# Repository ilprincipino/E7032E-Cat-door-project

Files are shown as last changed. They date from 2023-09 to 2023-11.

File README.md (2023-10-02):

# E7032E-Cat-door-project
Universal low power antennas for pet microchips
<p>
  
**Project members:** <br>
Matilda Segerlund, matseg-9@student.ltu.se  <br>
Nebez Rashid, nabras-9@student.ltu.se <br>
Anders Hagström, hagane-9@student.ltu.se <br>
Agnes Lindsten, agelin-7@student.ltu.se <br>
Arvid Mattsson, arvmat-9@student.ltu.se <br>
Jakob Ekvall, jakekv-9@student.ltu.se <br>

Link to report: [https://www.overleaf.com/read/vsyjcxfwmcch](https://www.overleaf.com/read/vsyjcxfwmcch) <br>

Link to presentation: https://docs.google.com/presentation/d/12QPiXXhClUaFdsH-6-YMc6YWno67U1GOmlV3GwxZOh8/edit?usp=sharing

Link to WBS/project plan: https://docs.google.com/spreadsheets/d/1j_RC8x2nzi24WwkHtlm5jIMLNItzt1e427vKWdE4rbc/edit?usp=sharing <br>

**Background:** <br>
Since the mid-80's, microchip implants have been used in pets and livestocks to identify them. These implements are a little larger than a rice grain. They are passive RFID chips that must be remotely powered to receive the identification information. They are progressively been required by law. <br>

Beside legal identification, these microchips can be used to identify a pet when they want to be fed (i.e., not allow an obese pet to over eat) or to let them enter or exit their home. The latter prevents "foreign" cats to enter homes where they have no business to be in. <br>

There is a problem when the orientation of the scanner's antenna and the microchips are not aligned. The pet doors and feeders are battery powered and fixed. The former results in not enough power to retrieve the information, while the latter could have been a solution by rotating the antenna (or chip inside the pet). <br>

**Objective:** <br>
The project is simply to design a low power antenna that allows the microchip to be read whatever is its relative orientation. <br>

**Key features:** <br>
* **Compatibility:** The solution must be ISO 11784 and ISO 11785 compliant. That is, it must be able to be optimized for 134.2 kHz, but should also be able to read at 125 kHz for US microchips.
* **Low power:** The cat door should work 6 months on four AA batteries.
* **Size:** It should fit in a pet door.
* **Temperature:** It should function in temperatures from -20°C to 60°C.
* **Internet ready:** The solution should be able to integrate a secured solution that connects to the Internet. This could include near field communication (NFC), bluetooth, and WiFi solutions. 

</p>

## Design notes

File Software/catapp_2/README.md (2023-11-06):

# catapp_2

A new Flutter project.

## Getting Started

This project is a starting point for a Flutter application.

A few resources to get you started if this is your first Flutter project:

- [Lab: Write your first Flutter app](https://docs.flutter.dev/get-started/codelab)
- [Cookbook: Useful Flutter samples](https://docs.flutter.dev/cookbook)

For help getting started with Flutter development, view the
[online documentation](https://docs.flutter.dev/), which offers tutorials,
samples, guidance on mobile development, and a full API reference.

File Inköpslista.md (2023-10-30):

| Date | Item |Amount | Link | Approved/ordered | Received | 
|---|---|---|---|---|---|
| 3/10 |Raspberry Pico W | 2 |https://www.electrokit.com/produkt/raspberry-pi-pico-wh/ | <ul><li>[X] </li></ul>  | <ul><li>[ ] </li></ul> | 
| 6/10 |Antenna wire | 1 |[https://www.elfa.se/sv/koppartrad-008mm-o0-1mm-200g-block-cul-200-10/p/15550334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](https://www.elfa.se/sv/koppartrad-2mm-o0-5mm-200g-block-cul-200-50/p/15550340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) | <ul><li>[x] </li></ul>  | <ul><li>[x] </li></ul> | 
| 6/10 |PCB  things from Farnell |34 items| I send an email with the basket and its also on git as "ShoppingBasket" | <ul><li>[x] </li></ul>  | <ul><li>[x] </li></ul> | 
| 30/10 |OP amp rekommenderad |1 items| https://se.farnell.com/microchip/mcp6l01ut-e-ot/ic-op-amp-1-0mhz-1-8v-sot23-5/dp/1852141?st=mcp6l01 | <ul><li>[x] </li></ul>  | <ul><li>[x] </li></ul> | 
| 30/10 |OP amp till breadboard |1 items| https://se.farnell.com/texas-instruments/lm358p/ic-op-amp-dual-dip8-358/dp/3117074?st=lm358  | <ul><li>[x] </li></ul>  | <ul><li>[x] </li></ul> | 

Företag som vi kan beställa ifrån: <br>
https://se.farnell.com/ <br>
https://www.rs-online.com/ <br>
https://www.elfa.se/sv/<br>

Ifall det inte finns på någon av de övre. <br>
https://www.digikey.se/en

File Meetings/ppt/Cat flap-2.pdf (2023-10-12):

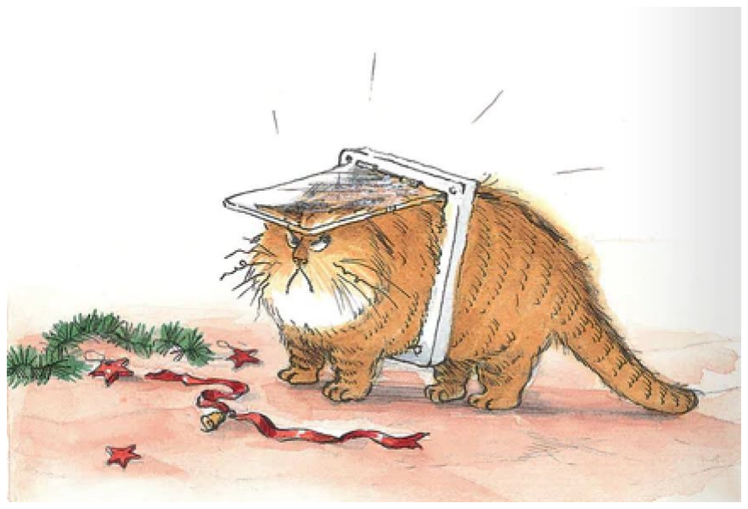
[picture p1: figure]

# Cat flap

# Agnes - IR sensors

- Rebuilt circuit
- More research
- Approved to order amplifier
- More test data
- Raspberry PI Pico / Thonny

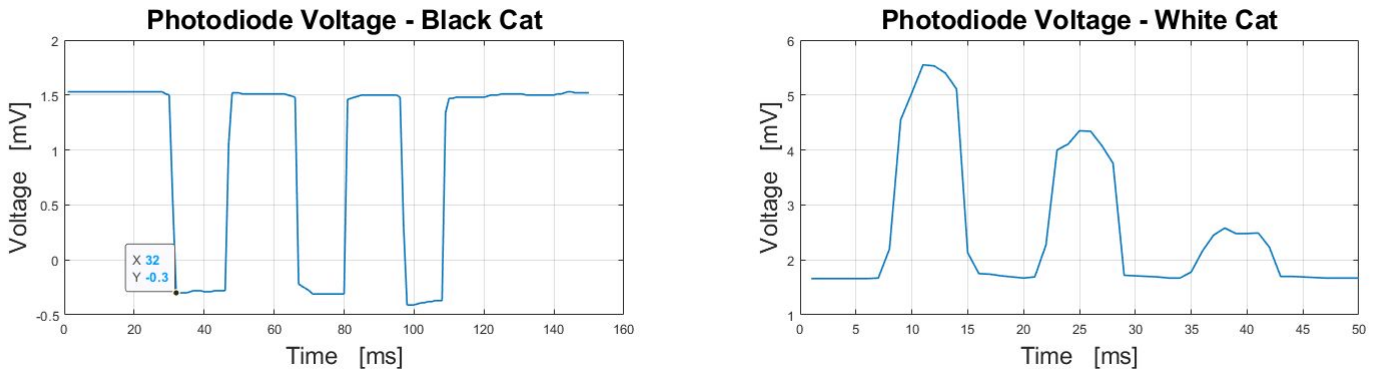
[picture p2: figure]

# Agnes - IR sensors

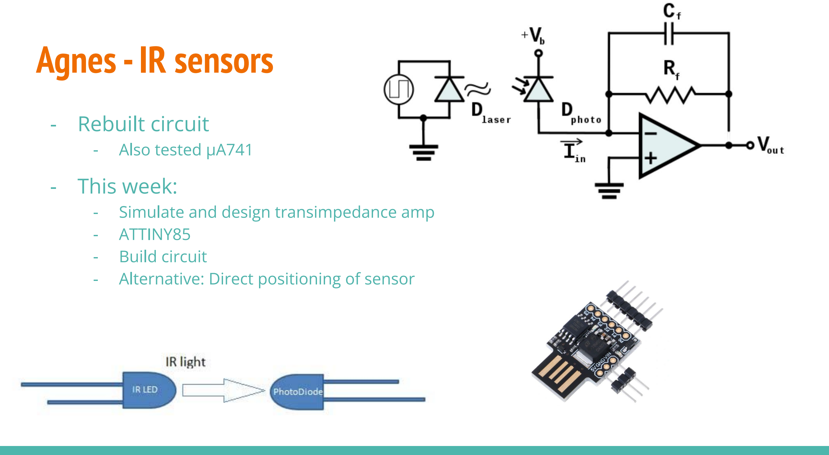
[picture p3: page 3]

- Rebuilt circuit
- Also tested μA741
- This week:
- Simulate and design transimpedance amp
- ATTINY85
- Build circuit
- Alternative: Direct positioning of sensor

# Nabaz - Application

Research about which framework should be used
- Django, Beeware, Kivy

Writing on the report
- Structure and writing about IR sensors

# Jakob & Arvid - Antenna

Circuit design and simulation.

Studying the measurements from the advanced oscilloscope.

# Jakob & Arvid - Antenna

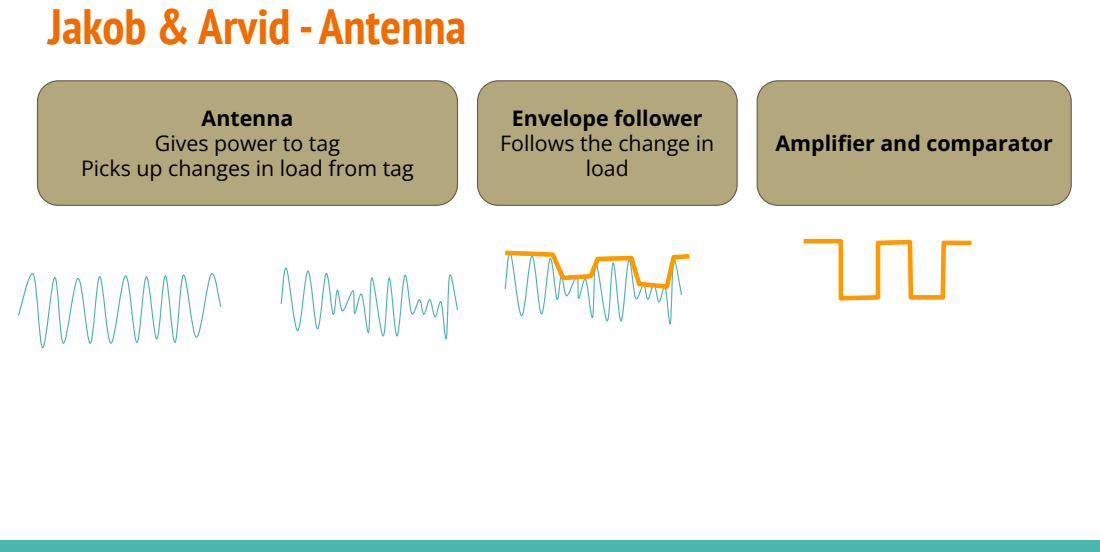
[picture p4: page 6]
load

Antenna
Gives power to tag
Picks up changes in load from tag

Envelope follower
Follows the change in

Amplifier and comparator

# Jakob & Anders

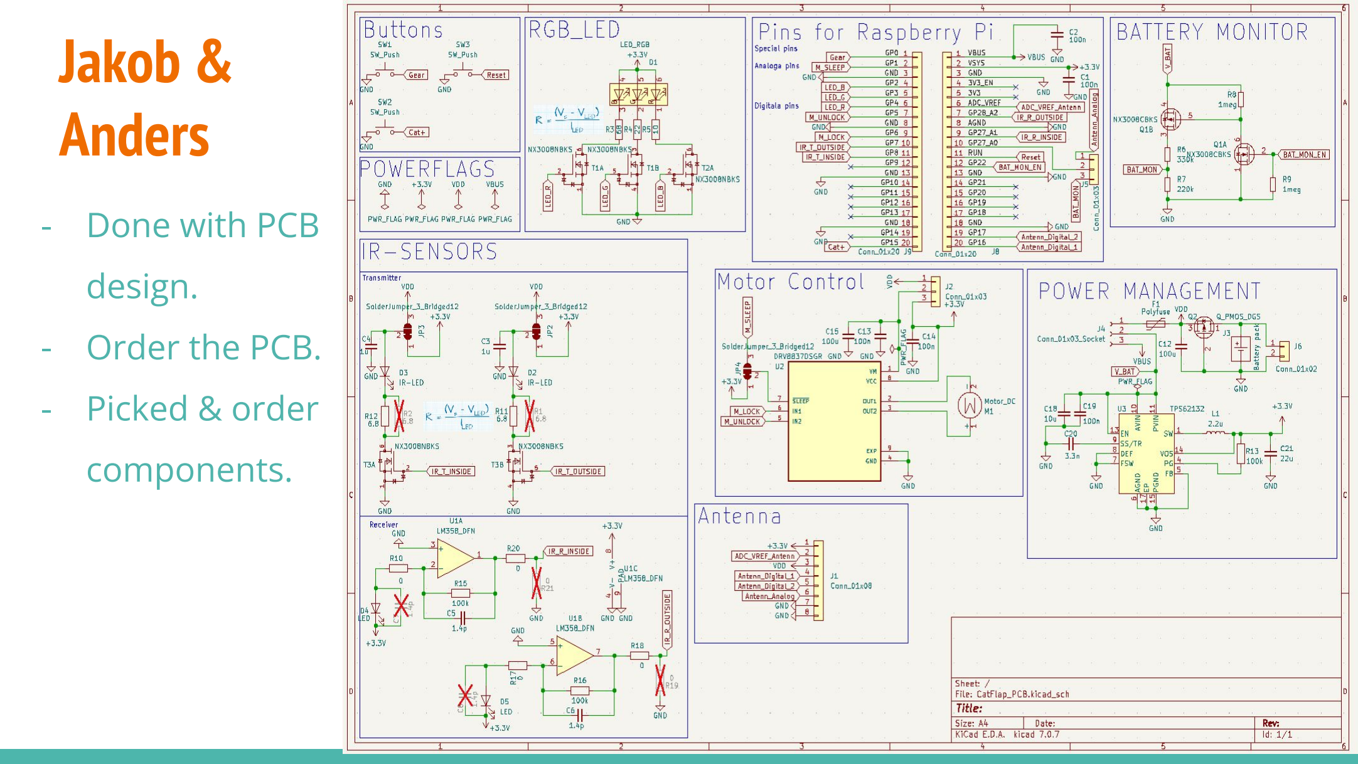
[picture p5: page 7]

- Done with PCB
design.
- Order the PCB.
- Picked & order
components.

# Jakob & Anders

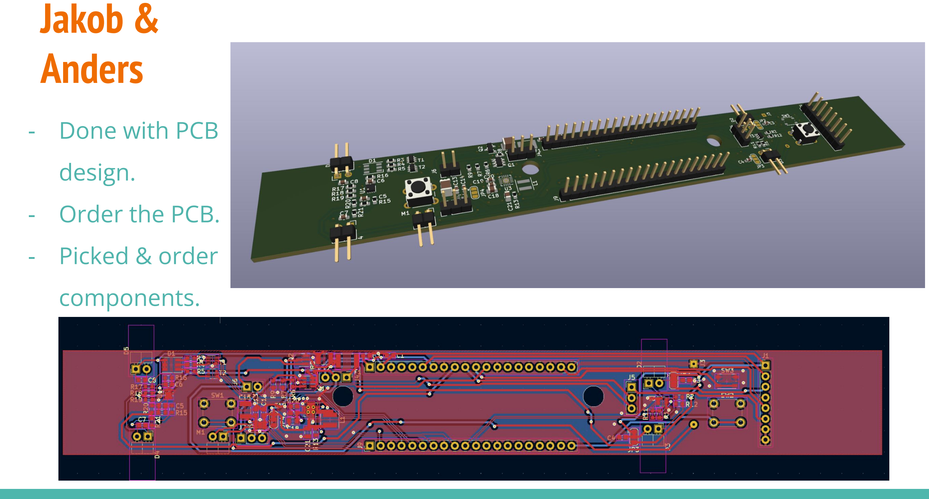
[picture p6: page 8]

- Done with PCB
design.
- Order the PCB.
- Picked & order
components.

# Anders & Matilda

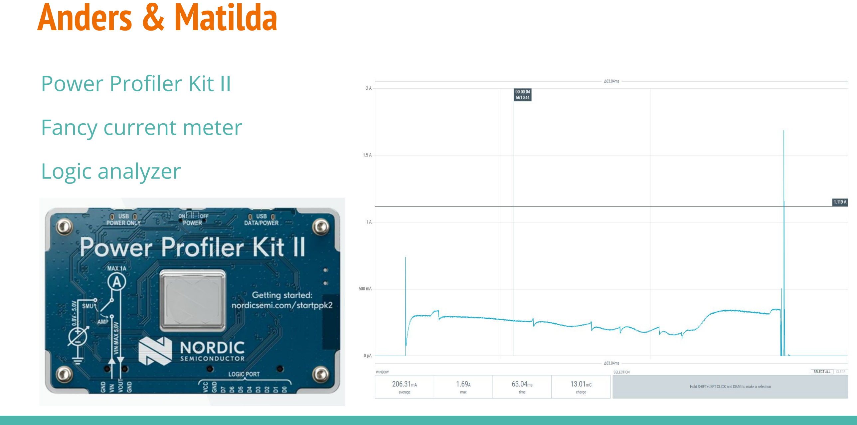
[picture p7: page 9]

Power Profiler Kit II
Fancy current meter
Logic analyzer

# Matilda

- Worked on sending/receiving data from the pi. Half gave up because of relevancy.
- Followed some tutorials to make a mobile app in Python
- Helped Anders with examining the motor using the power profile kit, gotten interesting results, had to hunt down Johan
- Random smaller tasks (planning, report, fixed small things in Git, meetings)

# Questions?

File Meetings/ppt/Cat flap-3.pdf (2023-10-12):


# Cat flap

# Agnes & Nabaz - IR sensors

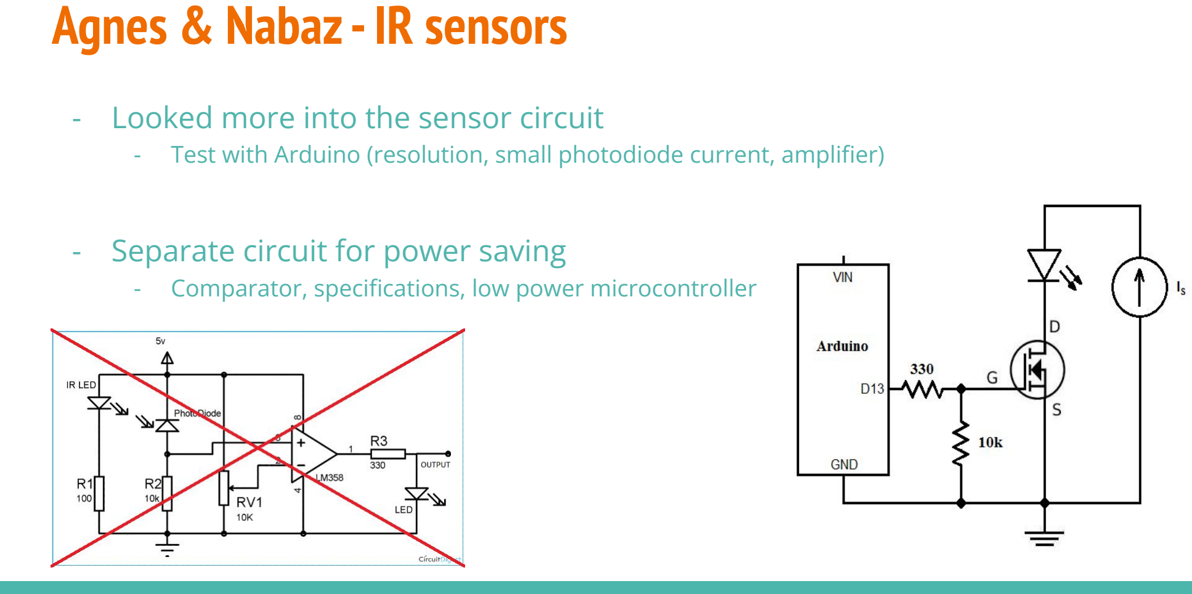
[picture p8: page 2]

- Looked more into the sensor circuit
- Test with Arduino (resolution, small photodiode current, amplifier)
- Separate circuit for power saving
- Comparator, specifications, low power microcontroller

# Agnes & Nabaz - IR sensors

- Tested actual current
- Multimeter. Quite dynamic response. Changing bias point?

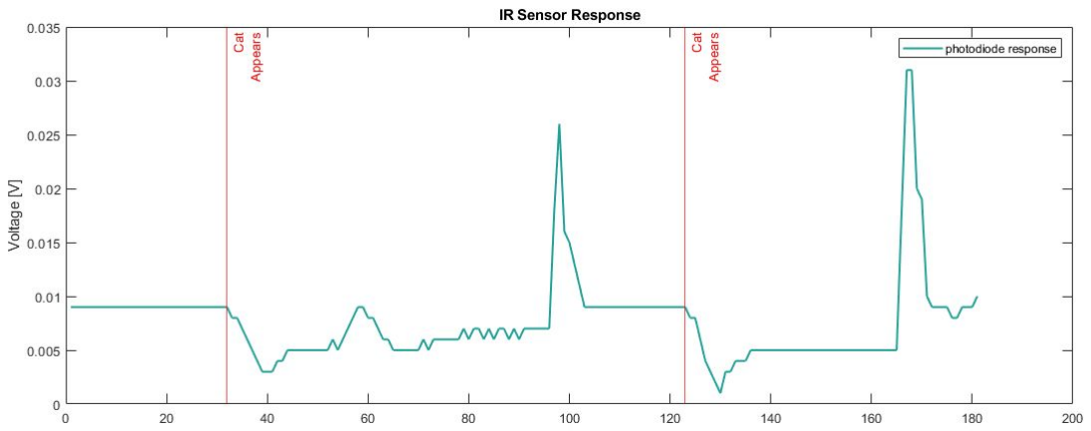
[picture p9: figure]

# Jakob & Arvid - Antenna

Finished designing, printing and assembling a rig to accurately measure the antennas range and effect of the tags angle relative to the cat flaps antenna.

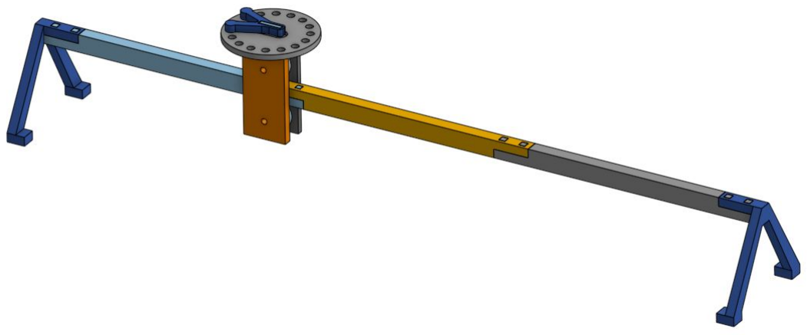
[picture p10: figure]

# Jakob & Anders

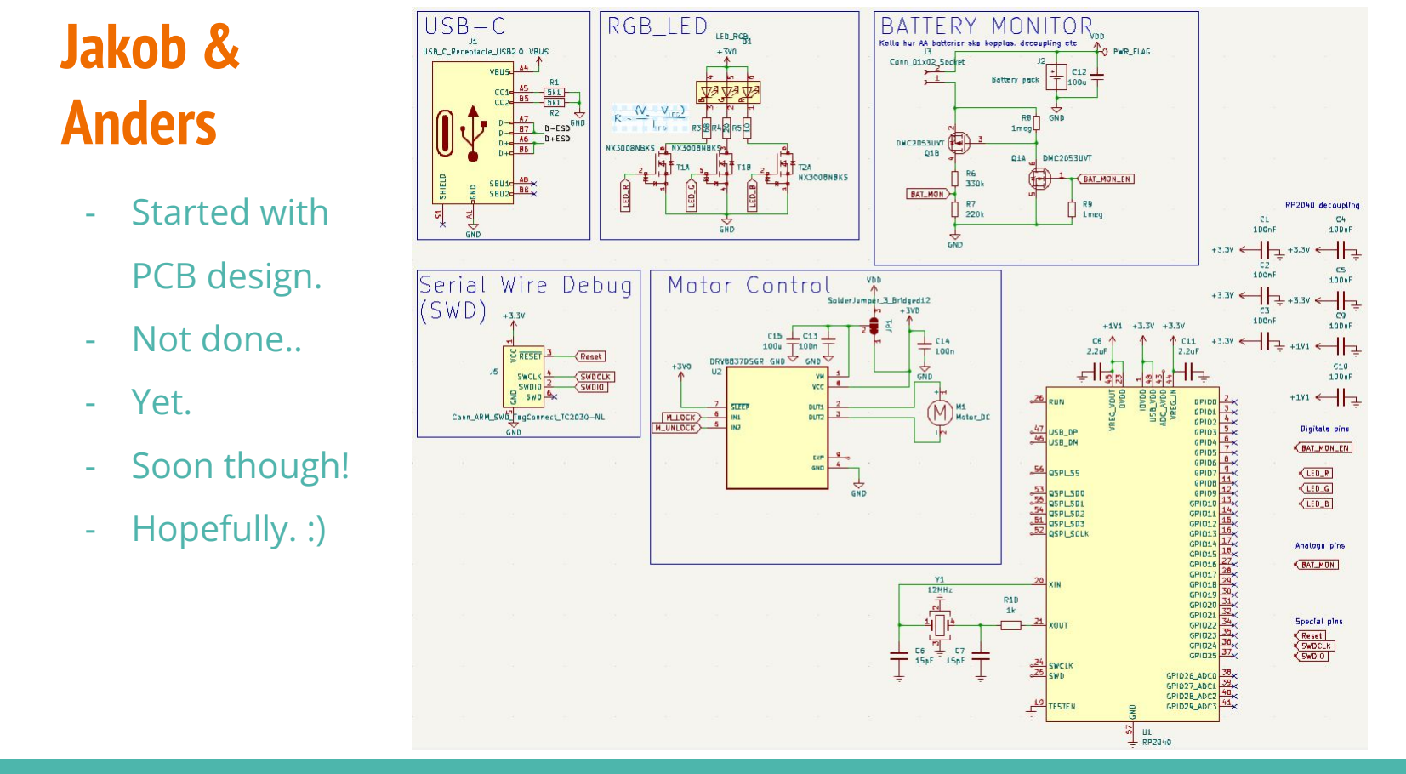
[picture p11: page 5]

- Started with
PCB design.
- Not done..
- Yet.
- Soon though!
- Hopefully. :)

# Matilda

- Worked on sending/receiving data from the pi. Half gave up because of relevancy. Broke the pi and rescued it.
- Followed some tutorials to make a mobile app in Python
- Soldered with Anders
- Helped Anders with examining the motor using the power profile kit, gotten interesting results, had to hunt down Johan
- Random smaller tasks (planning, report, fixed small things in Git, meetings)

# Questions?

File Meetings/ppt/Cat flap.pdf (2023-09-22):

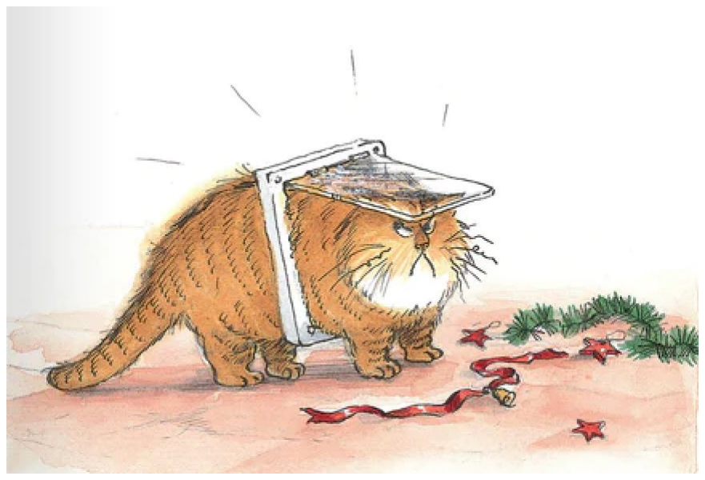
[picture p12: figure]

# Cat flap

# Agnes & Nabaz - IR sensors

- Created prototype for the sensor

# Agnes & Nabaz - IR sensors

- Created prototype for the sensor
- Measured the output from the receiver

# Agnes & Nabaz - IR sensors

- Created prototype for the sensor
- Measured the output from the receiver
- Stolen the sensors from the cat flap, replicated the results from the prototype

Agnes & Nabaz - IR sensors ⁻ Created prototype for the sensor
- Measured the output from the receiver
- Stolen the sensors from the cat flap, replicated the results from the prototype
- Research and Improvement
- Sensitivity
- Energy efficiency

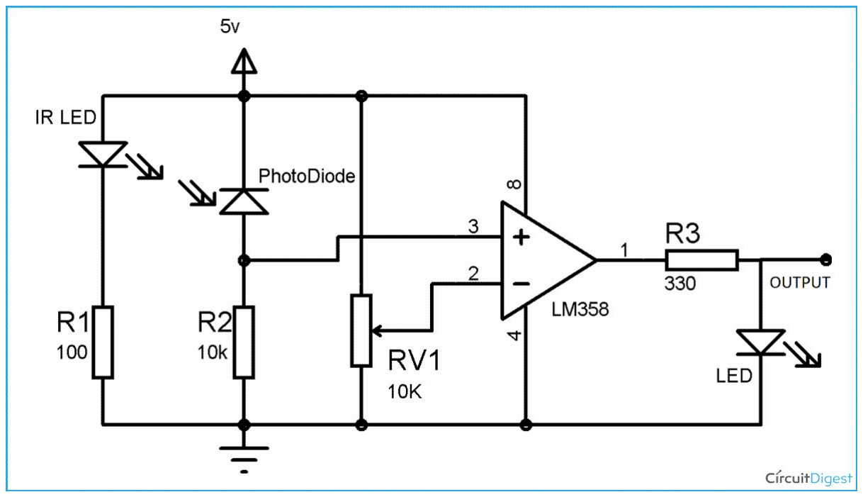
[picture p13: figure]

# Jakob & Arvid - Antenna

- Gained enough understanding RFID to start working on the new design

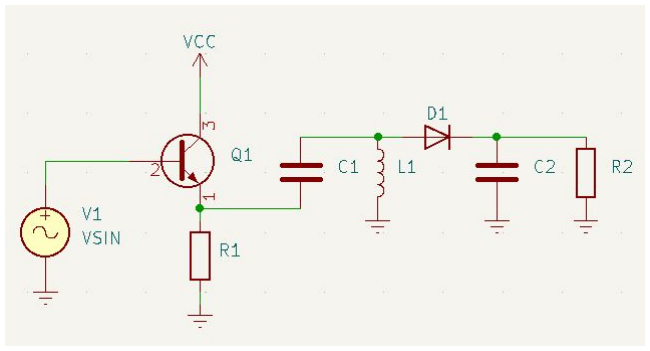
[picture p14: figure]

# Jakob & Arvid - Antenna

- Gained enough understanding RFID to start working on the new design
- Measured the signal of the pet microchip and antenna for further analysis

# Jakob & Arvid - Antenna

- Gained enough understanding RFID to start working on the new design
- Measured the signal of the pet microchip for further analysis
- Have started simulating on a preliminary design

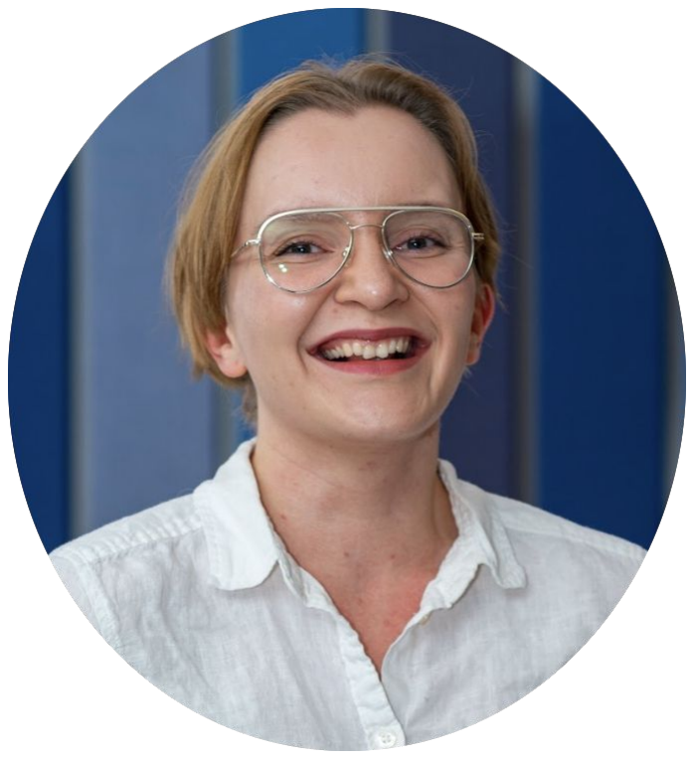
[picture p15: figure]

# Matilda & Anders - Motor

- H-bridge to control the direction of the motor

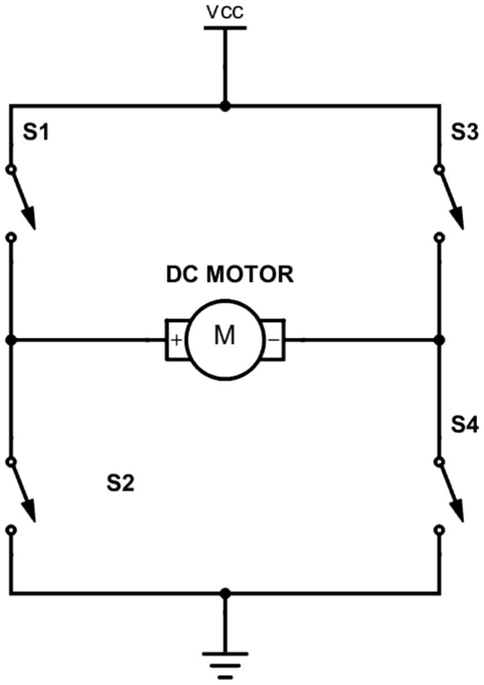
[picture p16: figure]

# Matilda & Anders - Motor

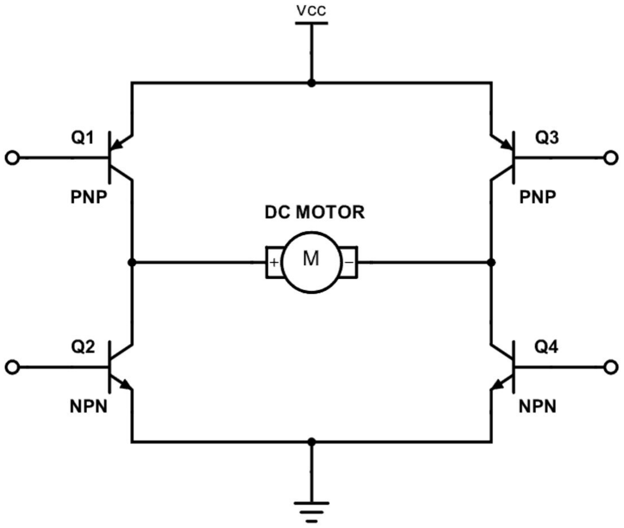
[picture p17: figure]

- H-bridge to control the direction of the motor
- NPN and PNP transistors

# Matilda & Anders - Motor

- H-bridge to control the direction of the motor
- NPN and PNP transistors
- Played around!

# Matilda & Anders - Motor

- H-bridge to control the direction of the motor
- NPN and PNP transistors
- Played around!
- Choices (DVR8837) + report

# Matilda & Anders - Motor

- H-bridge to control the direction of the motor
- NPN and PNP transistors
- Played around!
- Choices (DVR8837) + report
- Proper electric circuit →

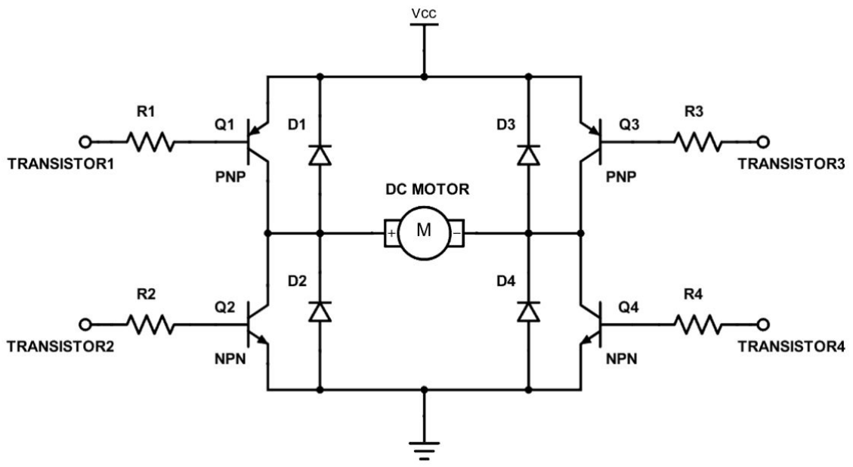
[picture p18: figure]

# Questions?

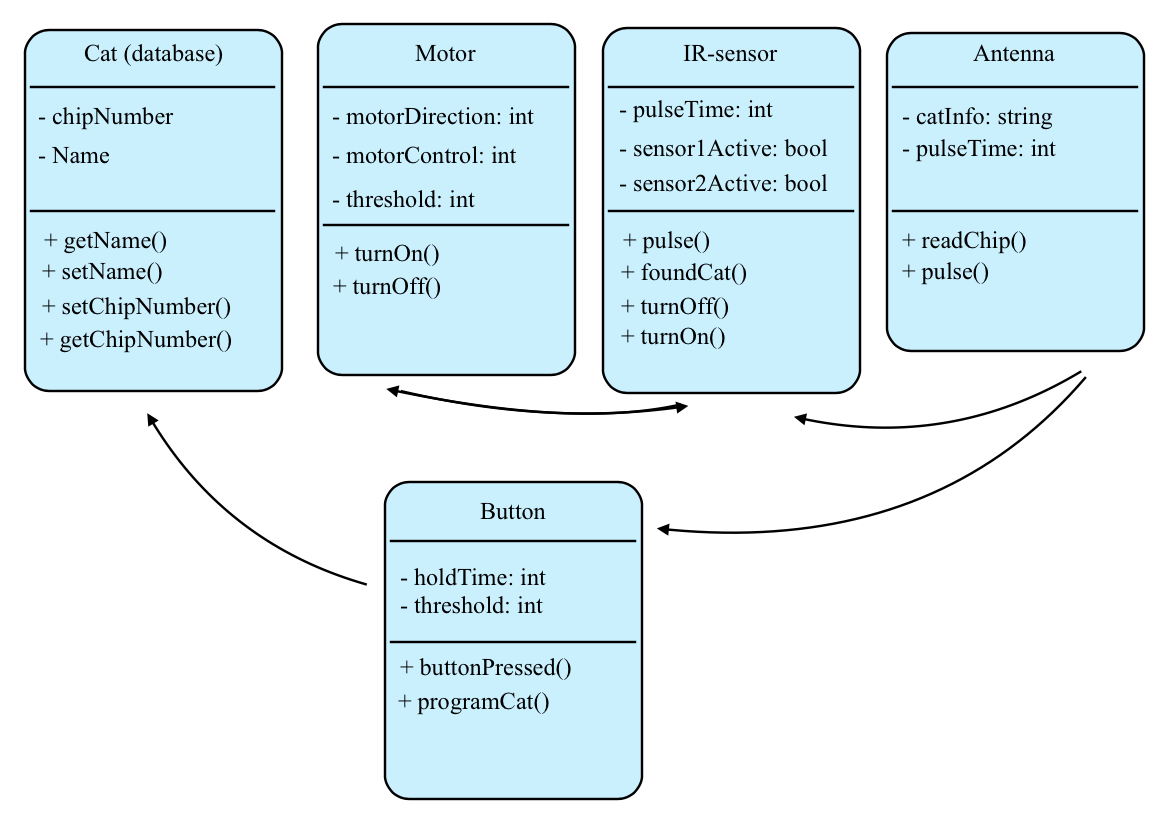
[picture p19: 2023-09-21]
Software/UML/Basic class diagram.png

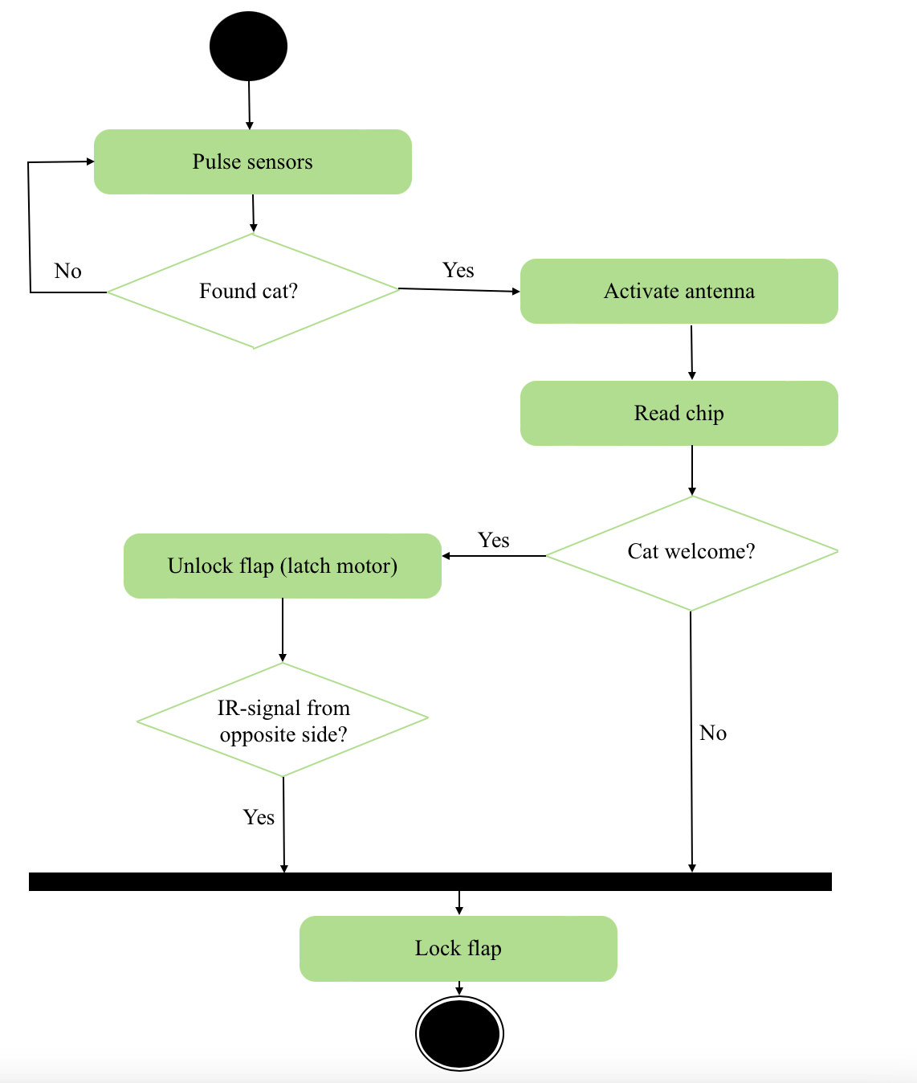
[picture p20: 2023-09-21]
Software/UML/Activity diagram.png

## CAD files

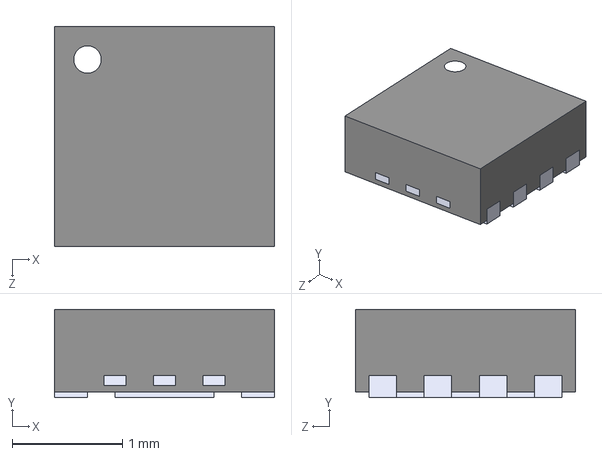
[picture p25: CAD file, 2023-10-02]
Hardware/Kicad/CAT FLAP/SnapEDA/DRV8837DSGR/DRV8837DSGR.step
2.00 x 0.8 x 2.00 mm

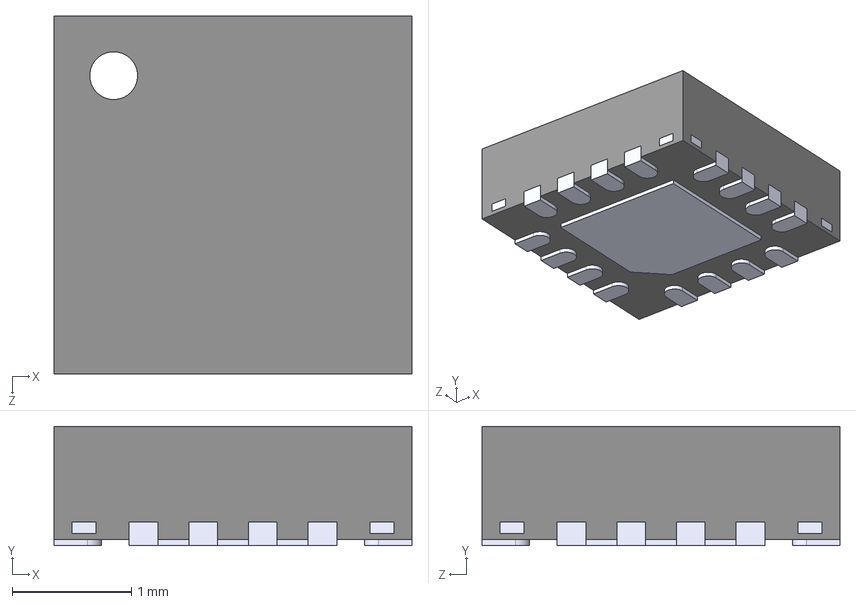
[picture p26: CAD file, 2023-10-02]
Hardware/Kicad/CAT FLAP/SnapEDA/TPS62132RGTR/TPS62132RGTR.step
3.00 x 1.00 x 3.00 mm

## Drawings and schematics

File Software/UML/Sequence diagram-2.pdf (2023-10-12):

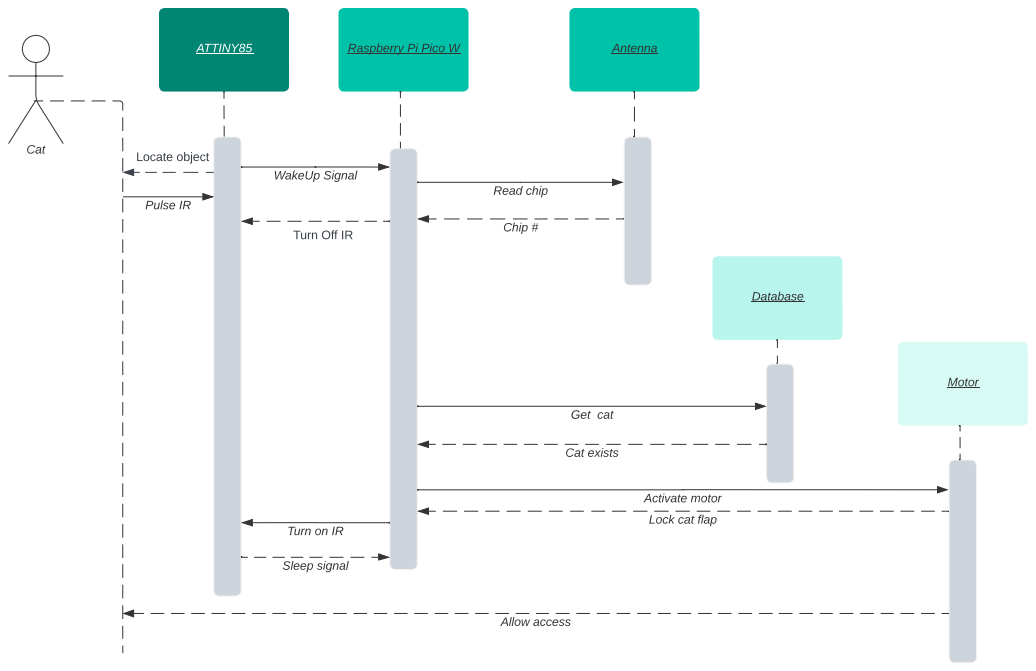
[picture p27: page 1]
ATTINY85; Raspberry Pi Pico W; Motor; Cat; Pulse IR; WakeUp Signal; Database; Allow access; Locate object; Antenna; Read chip; Chip #; Get cat; Cat exists; Sleep signal

Turn Off IR

Activate motor
Lock cat flap

Turn on IR

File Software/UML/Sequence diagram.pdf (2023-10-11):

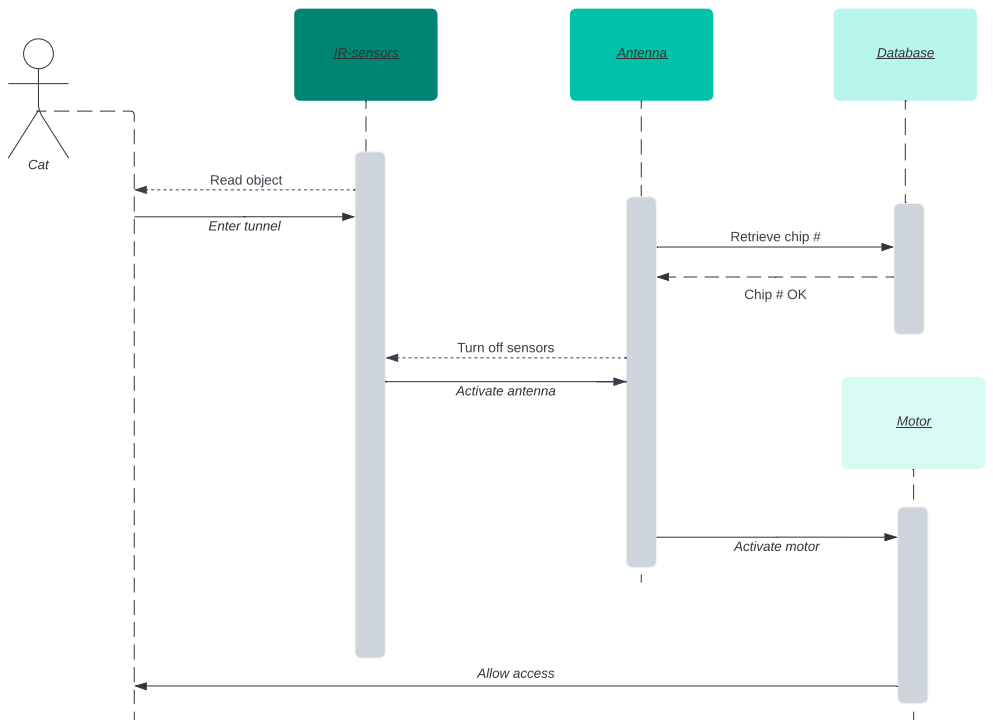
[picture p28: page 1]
IR-sensors; Antenna; Motor; Cat; Enter tunnel; Activate antenna; Read object; Database; Retrieve chip #; Chip # OK; Activate motor; Allow access

Turn off sensors

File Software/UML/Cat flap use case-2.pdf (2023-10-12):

### Cat flap

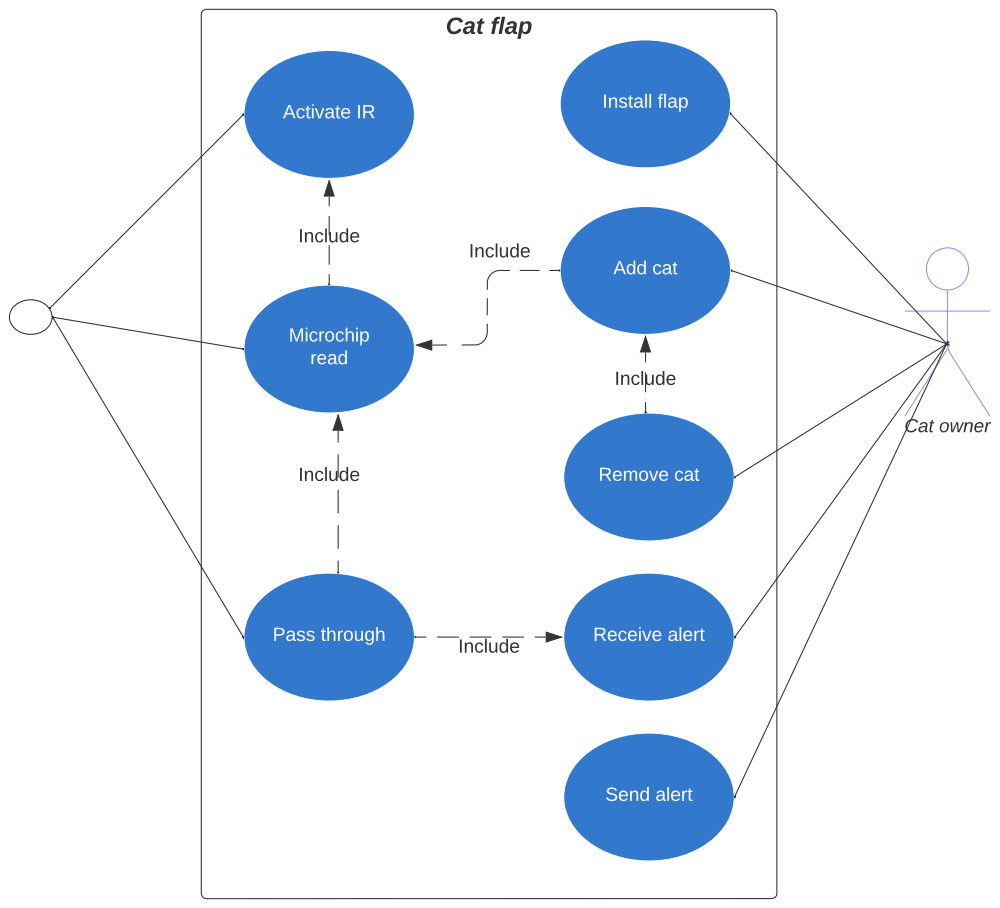
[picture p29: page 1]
Cat owner; Microchip read; Add cat; Remove cat; Install flap; Receive alert; Activate IR; Pass through; Include; Send alert

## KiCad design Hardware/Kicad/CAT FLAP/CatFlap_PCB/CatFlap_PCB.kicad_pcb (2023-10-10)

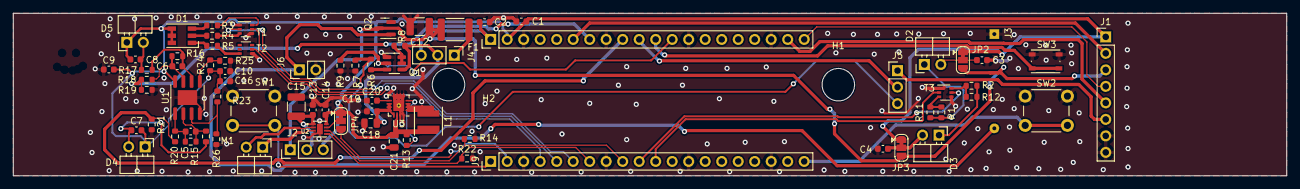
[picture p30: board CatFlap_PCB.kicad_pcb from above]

Board: 2 copper layers, 196.0 x 25.0 mm, 77 parts (0 on the bottom side), 56 nets.

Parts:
C1, C2, C10, C13, C14, C16, C19: 100n; C_0603_1608Metric
C3, C4, C9: 1u; C_0603_1608Metric
C5, C6, C7, C8: 1.4p; C_0603_1608Metric
C12, C15: 100u; C_1210_3225Metric
C18: 10u; C_0805_2012Metric
C20: 3.3n; C_0603_1608Metric
C21: 22u; C_0805_2012Metric
D1: LED_RGB; LED_RGB_PLCC-6
D2, D3: IR-LED; PinHeader_1x02_P2.54mm_Horizontal
D4, D5: LED; PinHeader_1x02_P2.54mm_Horizontal
F1: Polyfuse; Fuse_1812_4532Metric
H1, H2: MountingHole; MountingHole_5mm
J1: Conn_01x08; PinHeader_1x08_P2.54mm_Vertical
J2, J5: Conn_01x03; PinHeader_1x03_P2.54mm_Vertical
J3: Battery pack; BatteryHolder_MPD_BH-18650-PC2
J4: Conn_01x03_Socket; PinHeader_1x03_P2.54mm_Vertical
J6: Conn_01x02; PinHeader_1x02_P2.54mm_Vertical
J8, J9: Conn_01x20; PinHeader_1x20_P2.54mm_Vertical
JP2, JP3, JP4: SolderJumper_3_Bridged12; SolderJumper-3_P1.3mm_Bridged12_RoundedPad1.0x1.5mm
L1: 2.2u; L_Coilcraft_XxL4020
M1: Motor_DC; PinHeader_1x02_P2.54mm_Horizontal
Q1: NX3008CBKS; TSOT-23-6
Q2: Q_PMOS_DGS; SOT-23
R1, R2, R11, R12: 6.8; R_0603_1608Metric
R3: 68; R_0603_1608Metric
R4: 22; R_0603_1608Metric
R5: 10; R_0603_1608Metric
R6: 330k; R_0603_1608Metric
R7: 220k; R_0603_1608Metric
R8, R9: 1meg; R_0603_1608Metric
R10, R17, R18, R19, R20, R21: 0; R_0603_1608Metric
R13, R14, R15, R16, R22, R23, R24, R25, R26: 100k; R_0603_1608Metric
SW1, SW2: SW_Push; SW_PUSH_6mm_H4.3mm
SW3: SW_Push; SW_Push_1P1T_NO_Vertical_Wuerth_434133025816
T1, T2, T3: NX3008NBKS; SOT-363_SC-70-6
U1: LM358_DFN; SOIC-8-1EP_3.9x4.9mm_P1.27mm_EP2.29x3mm
U2: DRV8837DSGR; SON50P200X200X80-9N
U3: TPS62132; VQFN-16-1EP_3x3mm_P0.5mm_EP1.68x1.68mm_ThermalVias

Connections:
+3.3V: C1.2, C7.2, C8.2, C9.2, C10.2, C14.2, C16.2, C21.2, D1.4 (BA), D1.5 (GA), D1.6 (RA), D4.1 (K), D5.1 (K), J1.1, J2.3, J8.2, JP2.1 (A), JP3.1 (A), JP4.1 (A), L1.2, R13.2, R23.1, R24.1, U1.8 (V+), U2.8 (VCC), U3.14 (VOS)
/GP27_A0: J5.2, J8.10
ADC_VREF_Antenn: J1.2, J8.6
Antenn_Analog: J1.6, J5.1
Antenn_Digital_1: J1.4, J8.20
Antenn_Digital_2: J1.5, J8.19
BAT_MON: J5.3, R6.2, R7.1
BAT_MON_EN: J8.12, Q1.2 (G), R9.1
Cat+: J9.20, SW2.2
GND: C1.1, C2.1, C3.1, C4.1, C9.1, C10.1, C12.1, C13.1, C14.1, C15.1, C16.1, C18.1, C19.1, C20.2, C21.1, J1.7, J1.8, J3.1 (GND), J6.2, J8.3, J8.8, J8.13, J8.18, J9.3, J9.8, J9.13, J9.18, Q1.1 (S), Q2.2 (G), R7.2, R9.2, R14.2, R19.2, R21.2, R22.1, R25.2, R26.1, SW1.1, SW2.1, SW3.1, T1.1, T1.4, T2.1, T3.1, T3.4, U1.4 (V-), U1.9 (PAD), U2.4 (GND), U2.9 (EXP), U3.5 (FB), U3.6 (AGND), U3.7 (FSW), U3.8 (DEF), U3.15 (PGND), U3.16 (PGND), U3.17 (EP)
Gear: J9.1, SW1.2
IR_R_INSIDE: J8.9, R20.1, R21.1
IR_R_OUTSIDE: J8.7, R18.1, R19.1
IR_T_INSIDE: J9.11, T3.2
IR_T_OUTSIDE: J9.10, T3.5
LED_B: J9.4, T2.2
LED_G: J9.5, T1.5
LED_R: J9.6, T1.2
M_LOCK: J9.9, R14.1, U2.6 (IN1)
M_SLEEP: J9.2, JP4.3 (B)
M_UNLOCK: J9.7, R22.2, U2.5 (IN2)
unnamed: C5.1, R15.1, R20.2, U1.1
unnamed: C6.1, R16.1, R18.2, U1.7
unnamed: D1.3 (BK), R3.2
unnamed: D1.2 (GK), R4.2
unnamed: D1.1 (RK), R5.2
unnamed: C3.2, D2.2 (A), JP2.2 (C)
unnamed: D2.1 (K), R1.2, R11.2
unnamed: C4.2, D3.2 (A), JP3.2 (C)
unnamed: D3.1 (K), R2.2, R12.2
unnamed: C7.1, D4.2 (A), R10.2
unnamed: C8.1, D5.2 (A), R17.2
unnamed: C13.2, C15.2, J2.2, U2.1 (VM)
unnamed: J3.2 (V+), J6.1, Q2.1 (D)
unnamed: F1.1, J4.1
unnamed: JP4.2 (C), U2.7 (~SLEEP)
unnamed: L1.1, U3.1 (SW), U3.2 (SW), U3.3 (SW)
unnamed: M1.1 (+), U2.3 (OUT2)
unnamed: M1.2 (-), U2.2 (OUT1)
unnamed: Q1.5 (G), Q1.6 (D), R8.2
unnamed: Q1.3 (D), R6.1
unnamed: R1.1, R11.1, T3.3
unnamed: R3.1, T1.6
unnamed: R4.1, T1.3
unnamed: R5.1, T2.6
unnamed: R2.1, R12.1, T3.6
unnamed: R23.2, R26.2, U1.3 (+)
unnamed: C5.2, R10.1, R15.2, U1.2 (-)
unnamed: R24.2, R25.1, U1.5 (+)
unnamed: C6.2, R16.2, R17.1, U1.6 (-)
unnamed: R13.1, U3.4 (PG)
unnamed: C20.1, U3.9 (SS/TR)
Reset: J8.11, SW3.2
VBUS: C2.2, J4.3, J8.1
VDD: C12.2, F1.2, J1.3, J2.1, JP2.3 (B), JP3.3 (B), Q2.3 (S)
V_BAT: C18.2, C19.2, J4.2, Q1.4 (S), R8.1, U3.10 (AVIN), U3.11 (PVIN), U3.12 (PVIN), U3.13 (EN)

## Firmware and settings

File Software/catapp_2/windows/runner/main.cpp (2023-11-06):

#include <flutter/dart_project.h>
#include <flutter/flutter_view_controller.h>
#include <windows.h>

#include "flutter_window.h"
#include "utils.h"

int APIENTRY wWinMain(_In_ HINSTANCE instance, _In_opt_ HINSTANCE prev,
                      _In_ wchar_t *command_line, _In_ int show_command) {
  // Attach to console when present (e.g., 'flutter run') or create a
  // new console when running with a debugger.
  if (!::AttachConsole(ATTACH_PARENT_PROCESS) && ::IsDebuggerPresent()) {
    CreateAndAttachConsole();
  }

  // Initialize COM, so that it is available for use in the library and/or
  // plugins.
  ::CoInitializeEx(nullptr, COINIT_APARTMENTTHREADED);

  flutter::DartProject project(L"data");

  std::vector<std::string> command_line_arguments =
      GetCommandLineArguments();

  project.set_dart_entrypoint_arguments(std::move(command_line_arguments));

  FlutterWindow window(project);
  Win32Window::Point origin(10, 10);
  Win32Window::Size size(1280, 720);
  if (!window.Create(L"catapp_2", origin, size)) {
    return EXIT_FAILURE;
  }
  window.SetQuitOnClose(true);

  ::MSG msg;
  while (::GetMessage(&msg, nullptr, 0, 0)) {
    ::TranslateMessage(&msg);
    ::DispatchMessage(&msg);
  }

  ::CoUninitialize();
  return EXIT_SUCCESS;
}

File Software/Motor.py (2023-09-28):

from machine import Pin, Timer
import time

motor1 = Pin(19, Pin.OUT)
motor2 = Pin(20, Pin.OUT)
button2 = Pin(27, Pin.IN, Pin.PULL_DOWN)  #High button
button1 = Pin(21, Pin.IN, Pin.PULL_DOWN)  #Low button


def turnOn(motor_a, motor_b):
    motor_a.on()
    time.sleep(3)
    turnOff(motor_a)
    time.sleep(1)
    motor_b.on()
    time.sleep(3)
    turnOff(motor_b)
    
    
def turnOff(motor):
    motor.off()
    
#Using buttons for now, will get input from antenna later
while True:
    if button1.value() == 0 and button2.value() == 0:
        pass
    elif button1.value() == 1 and button2.value() == 0:
        turnOn(motor1, motor2)
    elif button2.value() == 1 and button1.value() == 0:
        turnOn(motor2, motor1)
    else:
        print("Don't wanna")

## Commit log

2023-09-10 Update sources about motor control.
2023-09-12 Create Motor
2023-09-12 Added arduino code for h-bro V1
2023-09-19 Create Hardware folder for Kicad files and Notes etc
2023-09-19 Added Kicad folder and included old mouse project
    [Mousetastic.kicad_sch, nPM1100.kicad_sch]
2023-09-19 I messed up again and again
    [Mousetastic.kicad_sch, nPM1100.kicad_sch]
2023-09-19 Added kicadfolder and cat flap and some old soluti
    [Mousetastic.kicad_sch, nPM1100.kicad_sch]
2023-09-19 Cleaned up CAT FLAP folder for future kicad files
2023-09-19 I messed up again, but now it worked :cheers:
    [Mousetastic.kicad_sch, nPM1100.kicad_sch]
2023-09-28 Python code for motor
    Will have to change input from buttons to antenna, and make sure motor works (not with LEDs)
2023-10-02 Updated Powermanagement
    [CatFlap_PCB.kicad_sch]
